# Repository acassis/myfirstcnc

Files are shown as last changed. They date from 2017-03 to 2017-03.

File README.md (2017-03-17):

# myfirstcnc
MyFirstCNC is an aluminum profile CNC:

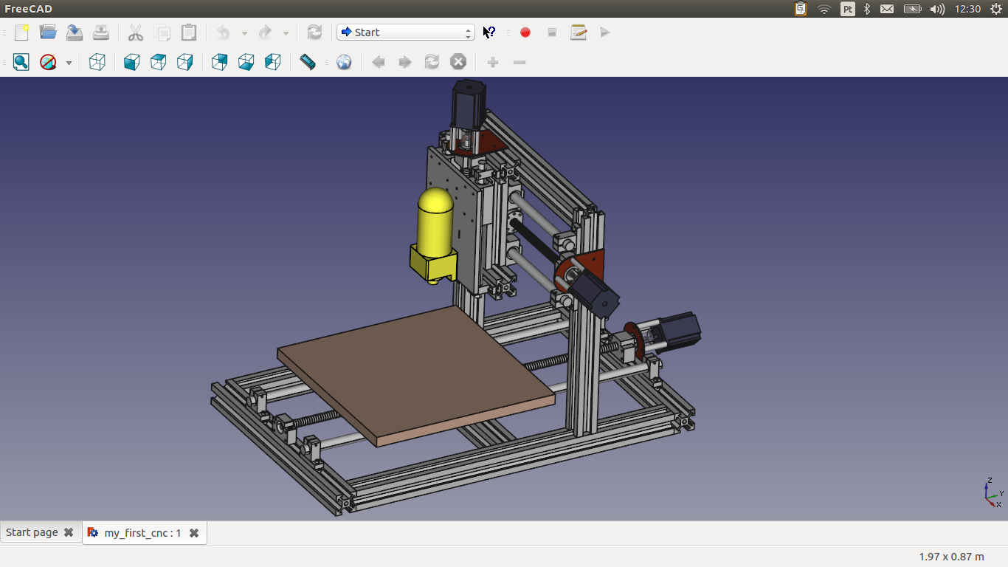
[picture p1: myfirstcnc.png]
MyFirstCNC


This CNC was designed using FreeCAD program:

https://www.freecadweb.org

Open the file Design/my_first_cnc.fcstd to see the complete
CNC machine.

Inside Design/Parts_FreeCAD/ you will find the CNC pieces that
were designed on FreeCAD and also the 2D design of parts you
will need to mill first to create your own CNC.

This project is based on Mogens Nicolaisen's CNC Router:
http://www.thingiverse.com/thing:41594

IMPORTANT NOTE: The ballnut_holder parts were based on the
ballnut housing I bought from eBay. I noticed they don't
have the exact same dimension. So, you need to double check
it before milling your ballnut_holders.

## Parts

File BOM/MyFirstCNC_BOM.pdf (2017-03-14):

Item | Quantity | Unit Price
45X45mm T-Slot:
45x45 T-Slot 180mm | 2 | $4.55
45x45 T-Slot 213mm | 2 | $5.40
45x45 T-Slot 413mm | 2 | $10.50
45x45 T-Slot 490mm | 2 | $12.40
45x45 T-Slot 503mm | 2 | $12.75
45x45 T-Slot 713mm | 2 | $18.05
M6 T-nut slot 10 | 40
M5 T-nut slot 10 | 10
| 12 | $1.38
200x230x10mm al-plate | 1 | $20.00
350x250x10mm al-plate | 1 | $30.00
SFC16 (SBR16 300mm) | 2 | $24.75
SFC20 (SBR20 500mm) | 2 | $36.96
SFC20 | 2 | $41.74
SK20 Shaft Support | 8 | $9.95
SK16 Shaft Support | 4 | $7.49
SBR16LUU (SC16WUU) | 2 | $15.50
SBR20UU (SC20VUU) | 8 | $6.91

Ballscrews RM1605:
RM1605 300mm | 1 | $42.80
RM1605 500mm | 1 | $52.30
RM1605 800mm | 1 | $170.48
| 3 | $47.42
Ball Nut Housings | 3 | $22.50
| 3 | $25.00
| 3 | $44.88
DeWalt D26670 | 1 | $99.00

Corner bracket + T-nut's and bolts

Hardened chrome-plated
shafts (Total length):

Sets BK/BF12 w/ locknuts and circlips

8mm X 8mm CNC Flexible Jaw Spider Plum Coupling

Stepper Motor 18.9Kgcm
57BYGH76-401A

6x mechanical limit switch

| 1 | RR$ 52.99
Motor Holder | 3 | R$ 9.80

Total:

2x line laser for laser crosshair

4 Axis 3.5A CNC TB6560
Stepper Motor Driver

Price | Status

$9.10
$10.80
$21.00
$24.80
$25.50
$36.10

$16.56

$20.00
$30.00

$49.50
$73.92
$83.48

$79.60
$29.96
$31.00
$55.28

$42.80
$52.30
$170.48

$142.26

$67.50

$180.00

$104.29

$99.00

$124.31

$73.50

$1,579.54 http://www.amazon.com/DEWALT-D26670-Laminate-Trim-Router/dp/B000HX6T28/www.ebay.com/itm/181028978193www.ebay.com/itm/370411712526www.ebay.com/itm/171052051646
www.ebay.com/itm/281102885725

http://www.aliexpress.com/store/product/High-quality-1pcs-SFU1605-Rolled-C7-Ball-Screw-L300mm-1pcs-Ballnut-ends-machining/714447_639644460.htmlhttp://www.aliexpress.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

http://www.ebay.com/itm/161242193610

http://www.ebay.com/itm/111221109249

http://www.ebay.com/itm/221277630019http://www.ebay.com/itm/360828125175

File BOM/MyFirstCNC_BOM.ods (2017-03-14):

Item | Quantity | Unit Price | Price | Status
45X45mm T-Slot:
45x45 T-Slot 180mm | 2 | $4.55 | $9.10
45x45 T-Slot 213mm | 2 | $5.40 | $10.80
45x45 T-Slot 413mm | 2 | $10.50 | $21.00
45x45 T-Slot 490mm | 2 | $12.40 | $24.80
45x45 T-Slot 503mm | 2 | $12.75 | $25.50
45x45 T-Slot 713mm | 2 | $18.05 | $36.10
M6 T-nut slot 10 | 40
M5 T-nut slot 10 | 10
Corner bracket + T-nut's and bolts | 12 | $1.38 | $16.56
200x230x10mm al-plate | 1 | $20.00 | $20.00
350x250x10mm al-plate | 1 | $30.00 | $30.00
Hardened chrome-plated shafts (Total length):
SFC16 (SBR16 300mm) | 2 | $24.75 | $49.50
SFC20 (SBR20 500mm) | 2 | $36.96 | $73.92
SFC20 | 2 | $41.74 | $83.48
SK20 Shaft Support | 8 | $9.95 | $79.60 |  | www.ebay.com/itm/181028978193
SK16 Shaft Support | 4 | $7.49 | $29.96 |  | www.ebay.com/itm/370411712526
SBR16LUU (SC16WUU) | 2 | $15.50 | $31.00 |  | www.ebay.com/itm/171052051646
SBR20UU (SC20VUU) | 8 | $6.91 | $55.28 |  | www.ebay.com/itm/281102885725
Ballscrews RM1605:
RM1605 300mm | 1 | $42.80 | $42.80 |  | http://www.aliexpress.com/store/product/High-quality-1pcs-SFU1605-Rolled-C7-Ball-Screw-L300mm-1pcs-Ballnut-ends-machining/714447_639644460.html
RM1605 500mm | 1 | $52.30 | $52.30 |  | http://www.aliexpress.com/store/product/1pcs-SFU1605-Ball-Screw-L500mm-1pcs-Ballnut-ends-machining/714447_648089331.html
RM1605 800mm | 1 | $170.48 | $170.48 |  | http://www.aliexpress.com/item/1pcs-SFU1605-Ball-Screw-L800mm-1pcs-Ballnut-ends-machining/648181573.html
Sets BK/BF12 w/ locknuts and circlips | 3 | $47.42 | $142.26 |  | http://www.ebay.com/itm/161242193610
Ball Nut Housings | 3 | $22.50 | $67.50 |  | http://www.ebay.com/itm/111221109249
8mm X 8mm CNC Flexible Jaw Spider Plum Coupling | 3 | $25.00 | $180.00 |  | http://www.ebay.com/itm/221277630019
Stepper Motor 18.9Kgcm 57BYGH76-401A | 3 | $44.88 | $104.29
DeWalt D26670 | 1 | $99.00 | $99.00 |  | http://www.amazon.com/DEWALT-D26670-Laminate-Trim-Router/dp/B000HX6T28/
6x mechanical limit switch
2x line laser for laser crosshair
4 Axis 3.5A CNC TB6560 Stepper Motor Driver | 1 | RR$ 52.99 | $124.31 |  | http://www.ebay.com/itm/360828125175
Motor Holder | 3 | R$ 9.80 | $73.50
Total: |  |  | $1,579.54

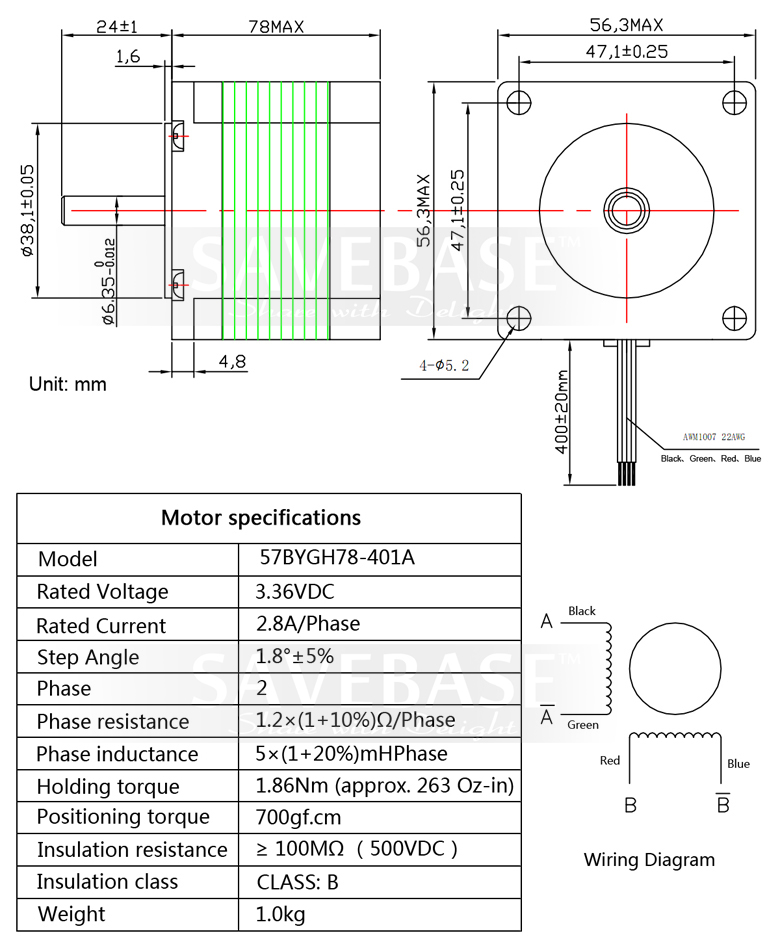
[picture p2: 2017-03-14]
Design/Parts_FreeCAD/stepper_motor/57BYGH78_401A.jpg

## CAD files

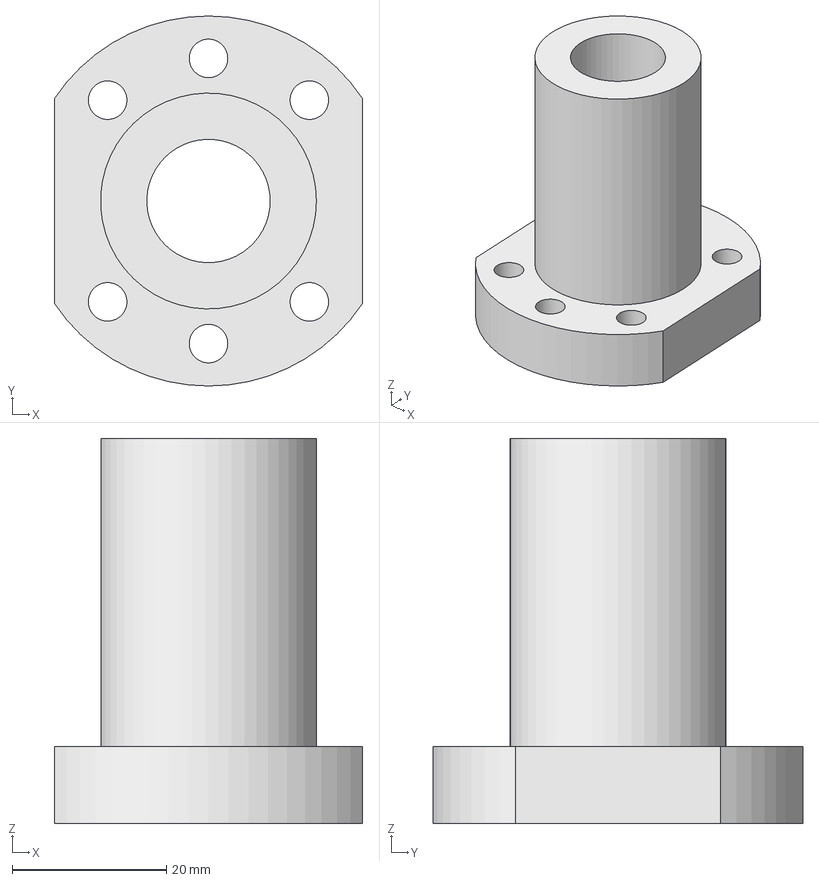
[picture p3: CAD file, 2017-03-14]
Design/Parts_FreeCAD/ballnut/ballnuts.fcstd
40.0 x 48.0 x 50.0 mm

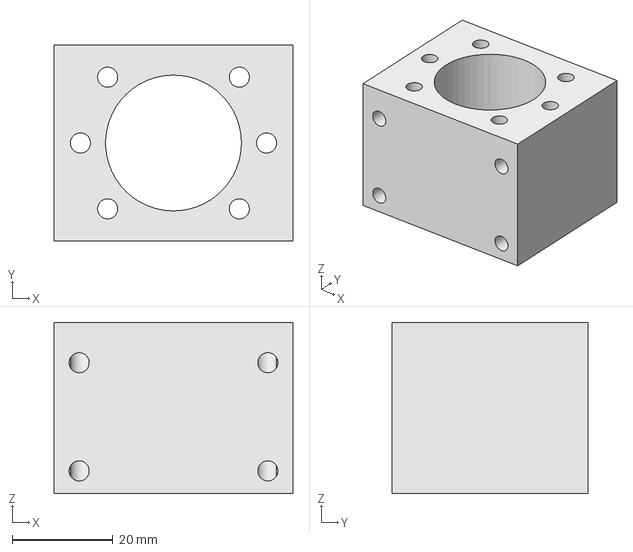
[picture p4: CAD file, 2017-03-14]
Design/Parts_FreeCAD/ballnut_house/ballnut_house.fcstd
47.5 x 39.0 x 34.0 mm

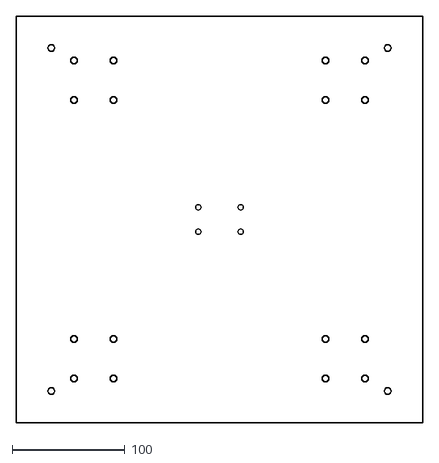
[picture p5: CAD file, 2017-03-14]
Design/Parts_FreeCAD/bed/bed_top_view.dxf
360.0 x 360.0

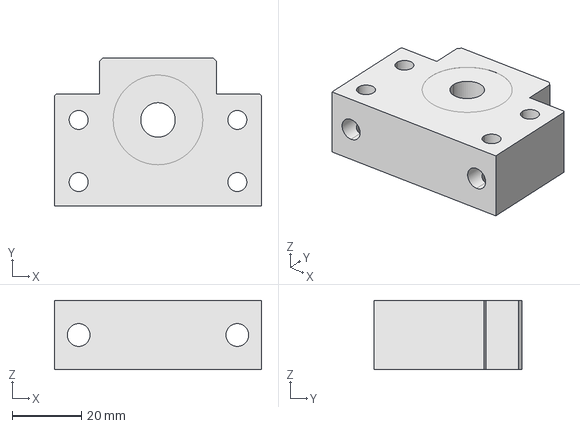
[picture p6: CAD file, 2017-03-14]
Design/Parts_FreeCAD/bf12/bf12.fcstd
60.0 x 43.0 x 20.0 mm

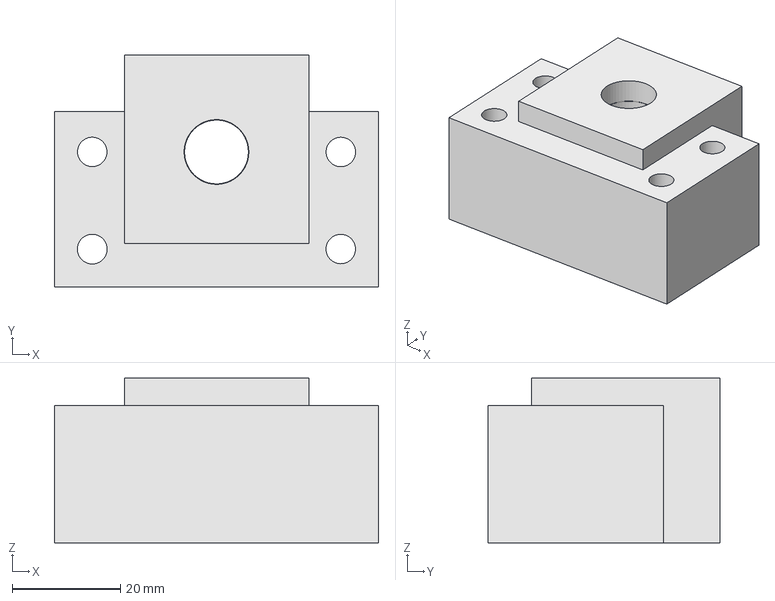
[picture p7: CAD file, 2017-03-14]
Design/Parts_FreeCAD/bk12/BK12.fcstd
60.0 x 42.9 x 30.5 mm

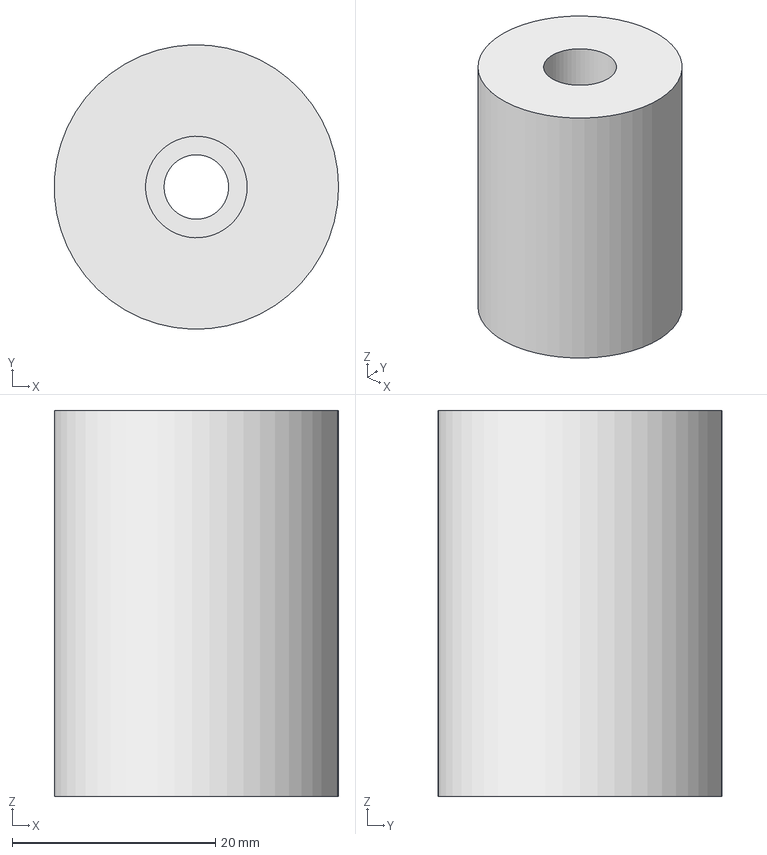
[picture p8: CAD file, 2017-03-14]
Design/Parts_FreeCAD/coupler/coupler.fcstd
28.0 x 28.0 x 38.0 mm

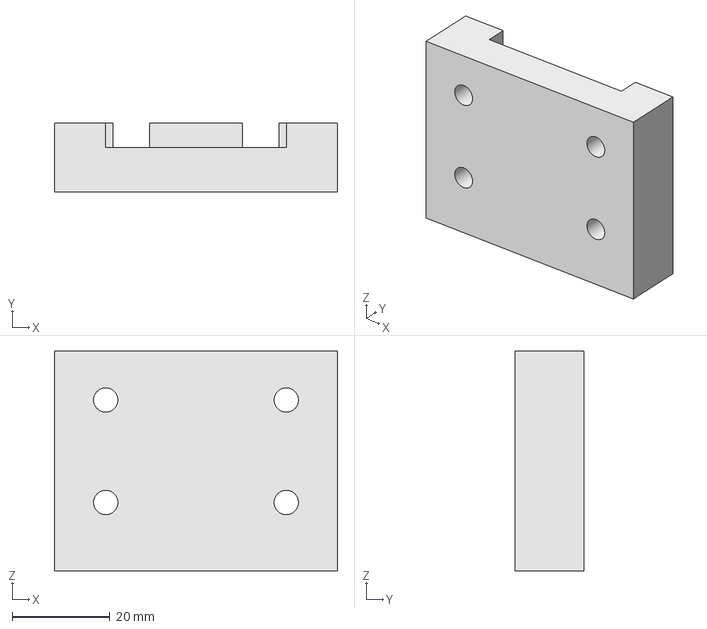
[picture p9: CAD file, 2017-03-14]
Design/Parts_FreeCAD/holder_ballnut_bed/ballnut_house_support.step
58.0 x 14.2 x 45.0 mm

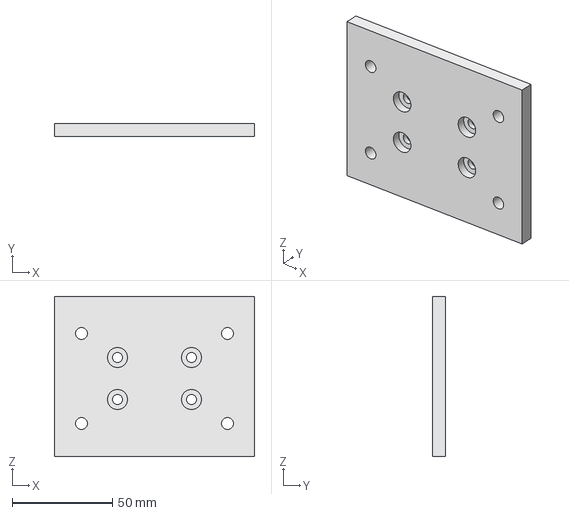
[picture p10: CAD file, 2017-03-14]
Design/Parts_FreeCAD/holder_ballnut_gantry/holder_ballnut_gantry.fcstd
100.0 x 6.50 x 80.0 mm

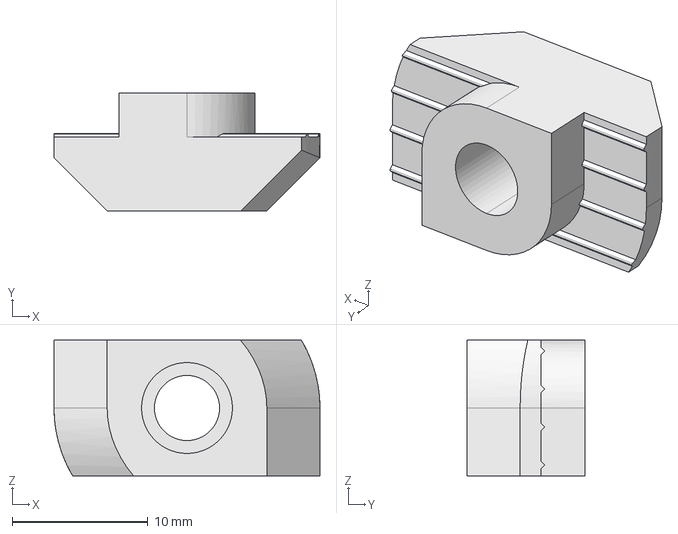
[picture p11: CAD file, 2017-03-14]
Design/Parts_FreeCAD/m6_tnut/m6_Tnut_slot10.fcstd
19.6 x 8.70 x 10.0 mm

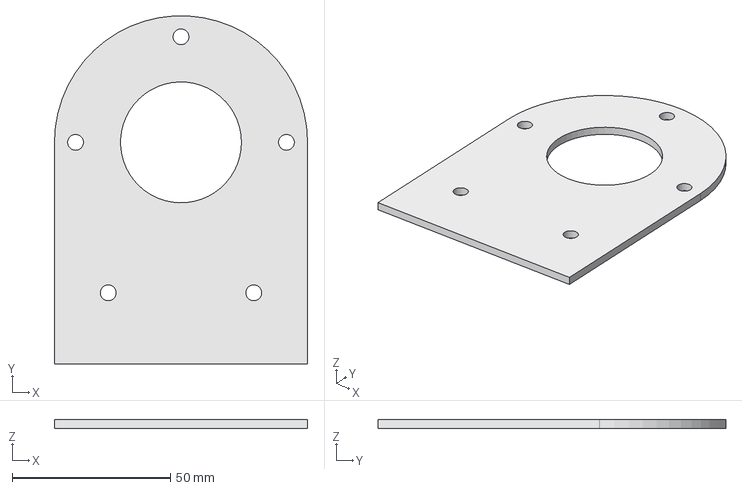
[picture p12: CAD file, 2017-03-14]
Design/Parts_FreeCAD/motor_base/motor_base.step
80.0 x 110.0 x 2.70 mm

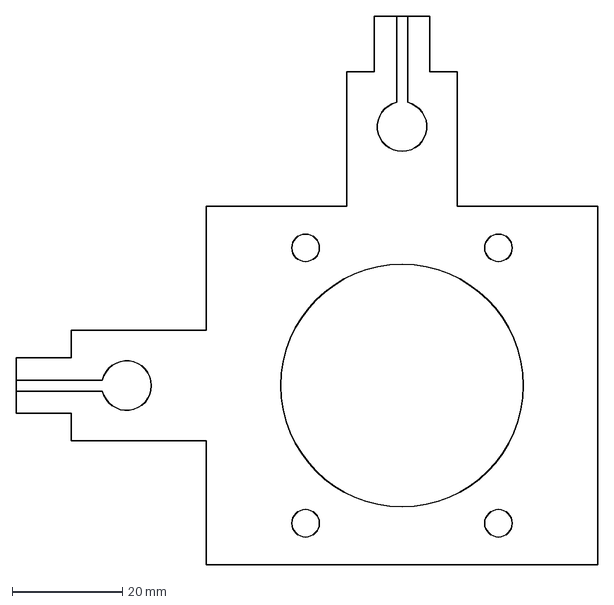
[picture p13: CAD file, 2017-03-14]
Design/Parts_FreeCAD/original/laserholder.dxf
105.5 x 99.5 mm

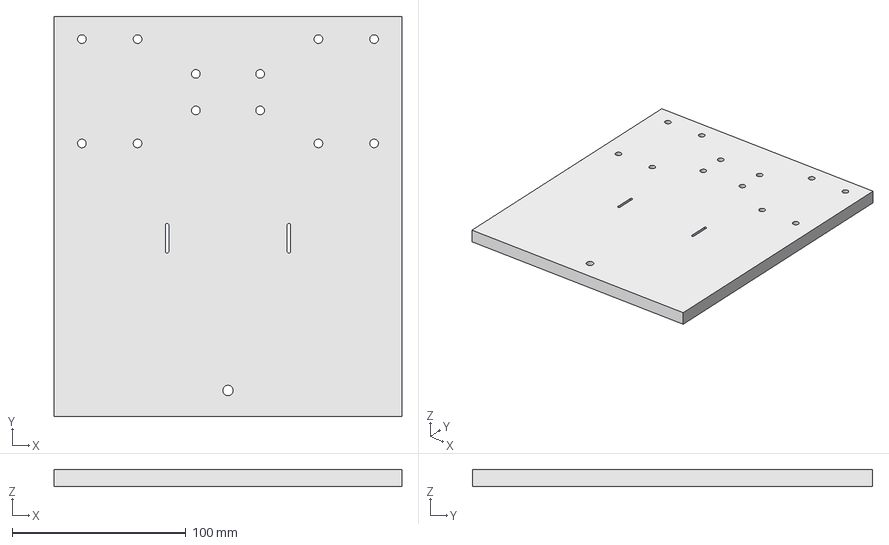
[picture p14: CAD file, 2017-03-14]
Design/Parts_FreeCAD/platez_base/platez_base.fcstd
200.0 x 230.0 x 10.0 mm

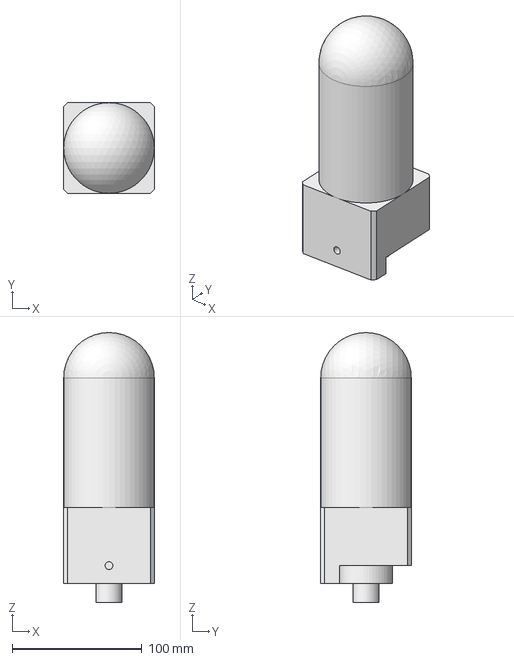
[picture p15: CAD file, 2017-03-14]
Design/Parts_FreeCAD/router/router.fcstd
70.0 x 70.0 x 208.5 mm

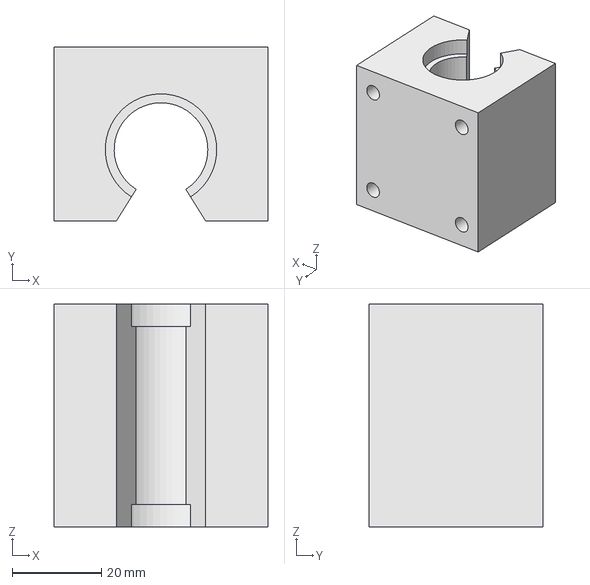
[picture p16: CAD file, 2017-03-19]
Design/Parts_FreeCAD/sbr20uu/sbr20uu.fcstd
48.0 x 39.0 x 50.0 mm

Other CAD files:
Design/Parts_FreeCAD/sc16wuu/sc16wuu.fcstd
Design/Parts_FreeCAD/sc20vuu/SC20VUU.fcstd
Design/Parts_FreeCAD/sk16/sk16.fcstd
Design/Parts_FreeCAD/sk20/sk20.fcstd
Design/Parts_FreeCAD/ballscrew/ballscrew_thread.fcstd
Design/Parts_FreeCAD/ballscrew/rm1605_800mm.fcstd
Design/Parts_FreeCAD/ballscrew/simple_ballscrew.fcstd
Design/Parts_FreeCAD/ballscrew/simple_ballscrew_300mm.fcstd
Design/Parts_FreeCAD/ballscrew_500mm/simple_ballscrew_500mm.fcstd
Design/Parts_FreeCAD/bed/bed.dwg
Design/Parts_FreeCAD/bed/bed.fcstd
Design/Parts_FreeCAD/bed/bed.step
Design/Parts_FreeCAD/holder_ballnut_bed/ballnut_house_support.dxf
Design/Parts_FreeCAD/holder_ballnut_bed/ballnut_house_support.fcstd
Design/Parts_FreeCAD/motor_base/Motor_Base.fcstd
Design/Parts_FreeCAD/motor_base/motor_base.dxf
Design/Parts_FreeCAD/original/BedAndMotorMount.dxf
Design/Parts_FreeCAD/original/pladez.dxf
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

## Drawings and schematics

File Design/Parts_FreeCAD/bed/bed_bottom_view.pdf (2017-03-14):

298mm

35mm

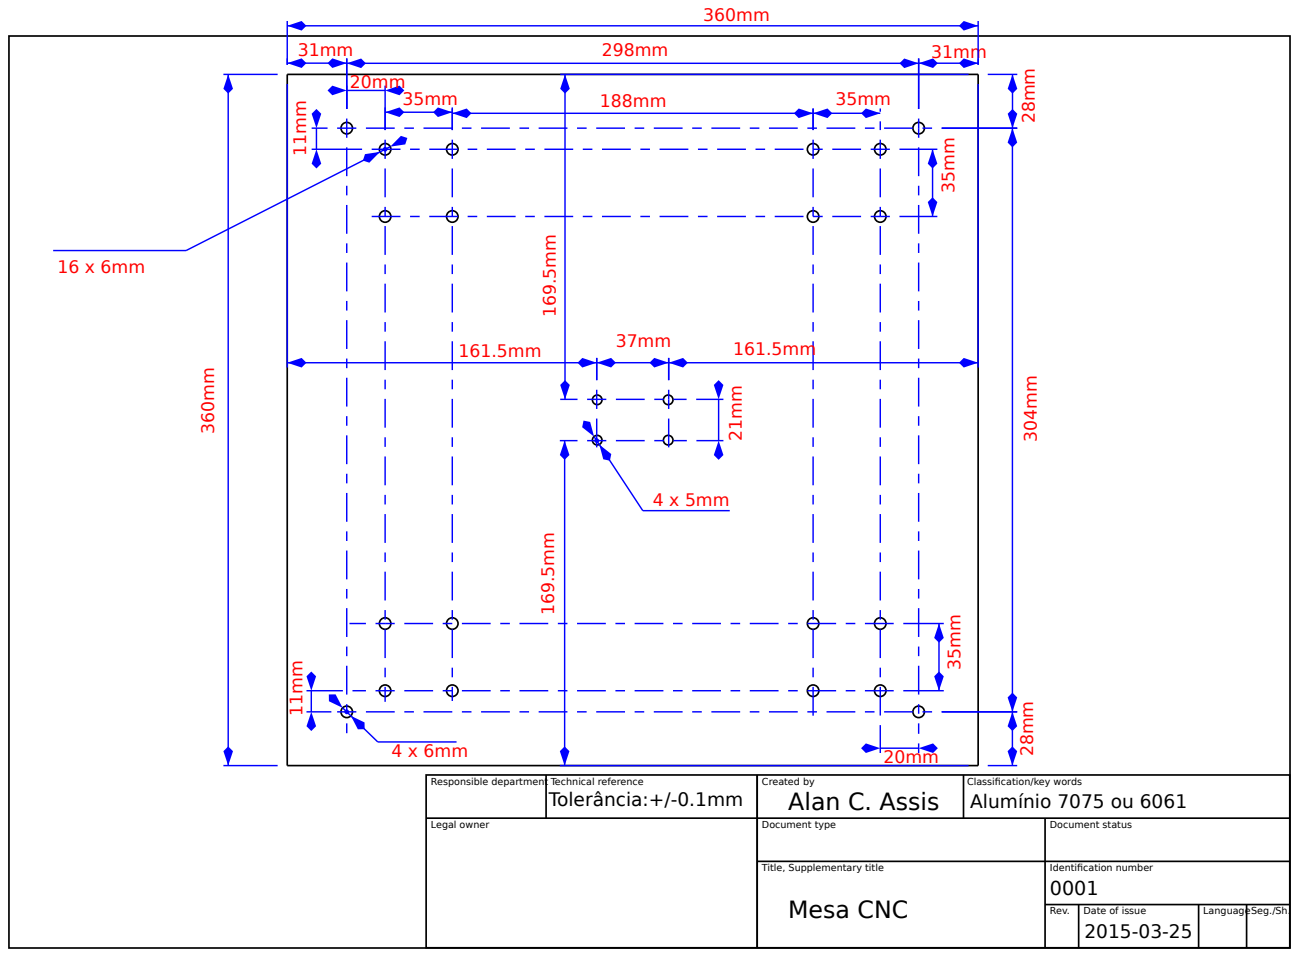
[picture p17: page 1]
161.5mm 169.5mm ¹⁶⁹.5mm; Responsible department Technical reference; Created by; Classification/key words; Legal owner; Document type; Document status; Title, Supplementary title; Identification number; Rev.; Date of issue; LanguageSeg./Sh.; Alan C. Assis; Mesa CNC; Tolerância:+/-0.1mm; Alumínio 7075 ou 6061

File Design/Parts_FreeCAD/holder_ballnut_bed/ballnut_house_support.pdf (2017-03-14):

58mm

12mm | 19mm | 12mm

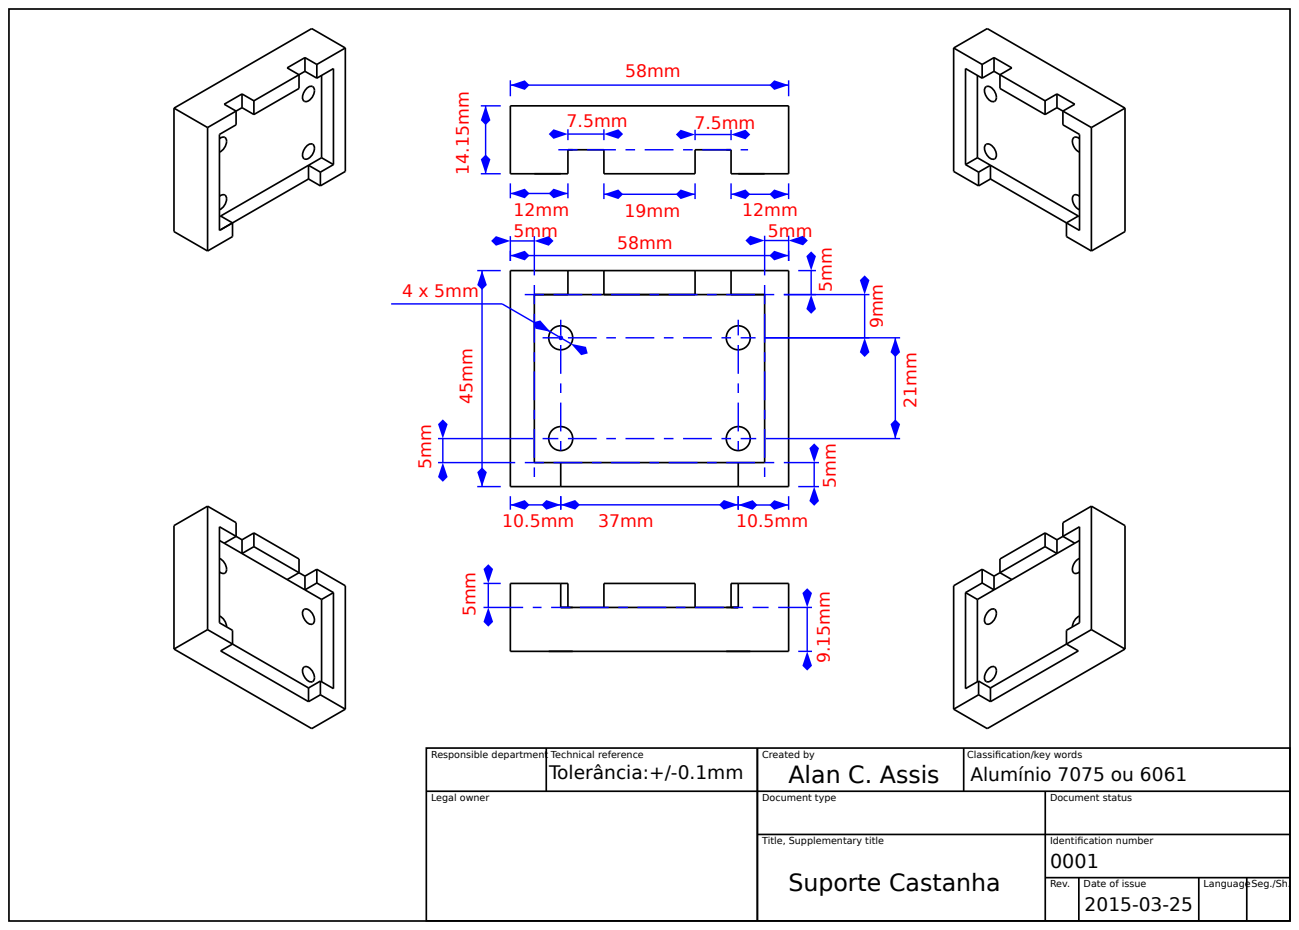
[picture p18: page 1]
Responsible department Technical reference; Created by; Classification/key words; Legal owner; Document type; Document status; Title, Supplementary title; Identification number; Rev.; Date of issue; LanguageSeg./Sh.; Alan C. Assis; Suporte Castanha; Tolerância:+/-0.1mm; Alumínio 7075 ou 6061

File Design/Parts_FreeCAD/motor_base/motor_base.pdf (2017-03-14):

33.35mm

# 5 x 5mm

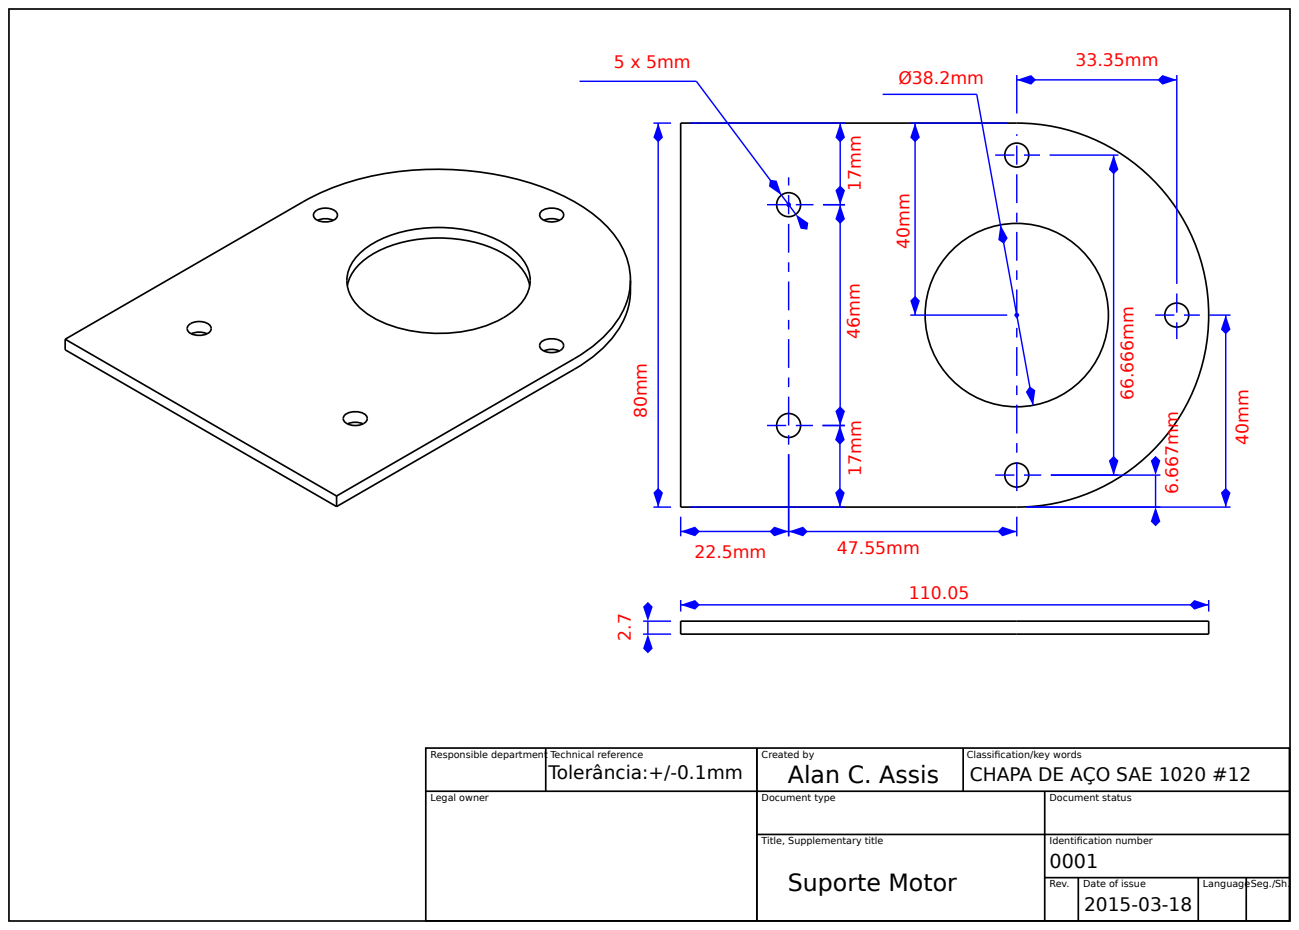
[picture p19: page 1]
Responsible department Technical reference; Created by; Classification/key words; Legal owner; Document type; Document status; Title, Supplementary title; Identification number; Rev.; Date of issue; LanguageSeg./Sh.; Alan C. Assis; Suporte Motor; Tolerância:+/-0.1mm; CHAPA DE AÇO SAE 1020 #12

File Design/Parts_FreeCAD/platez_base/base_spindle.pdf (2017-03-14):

16mm 32mm | 32mm 16mm 21mm
104mm

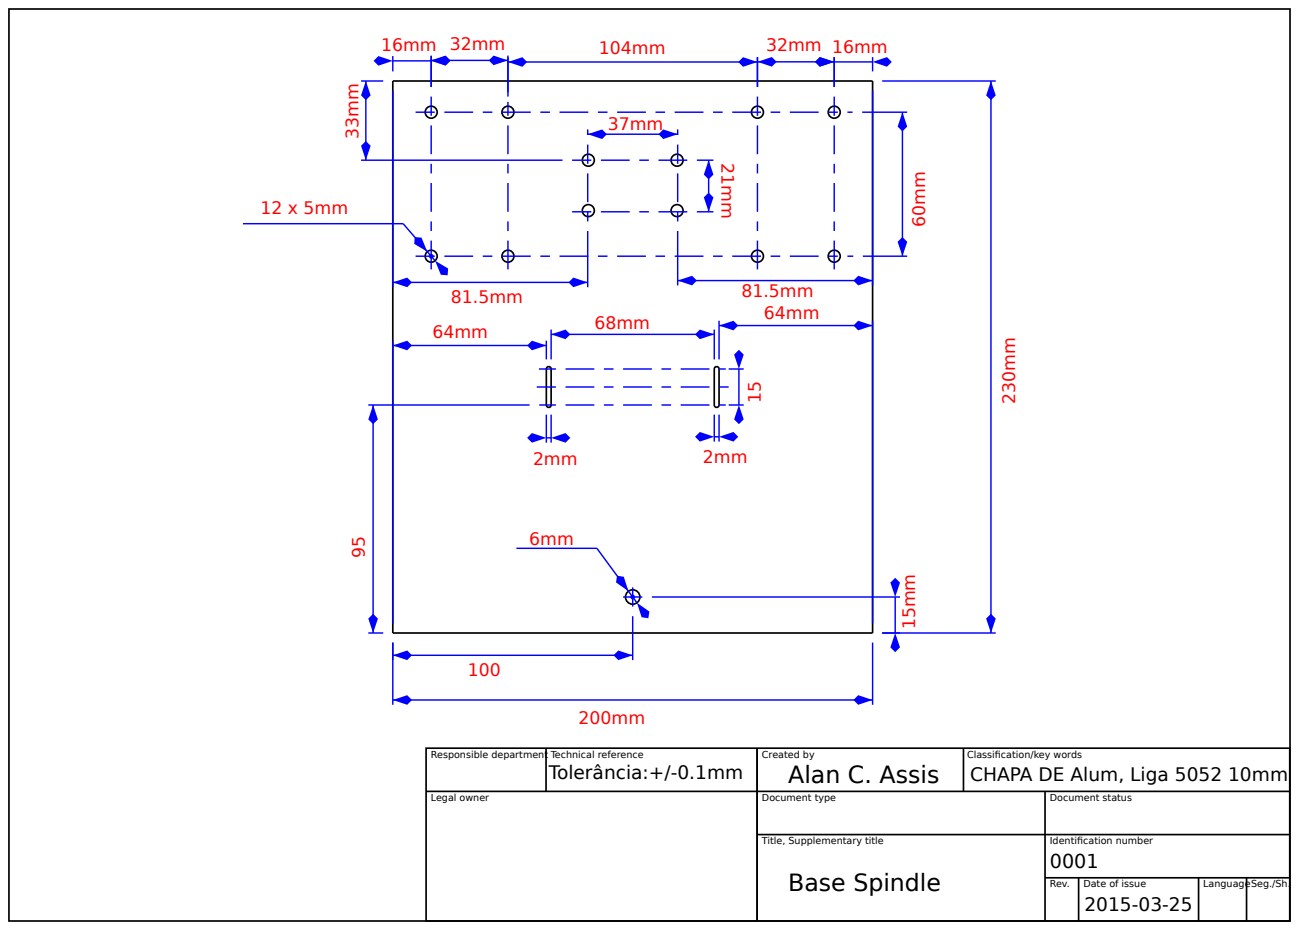
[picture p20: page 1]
Responsible department Technical reference; Created by; Classification/key words; Legal owner; Document type; Document status; Title, Supplementary title; Identification number; Rev.; Date of issue; LanguageSeg./Sh.; Alan C. Assis; Base Spindle; Tolerância:+/-0.1mm; CHAPA DE Alum, Liga 5052 10mm

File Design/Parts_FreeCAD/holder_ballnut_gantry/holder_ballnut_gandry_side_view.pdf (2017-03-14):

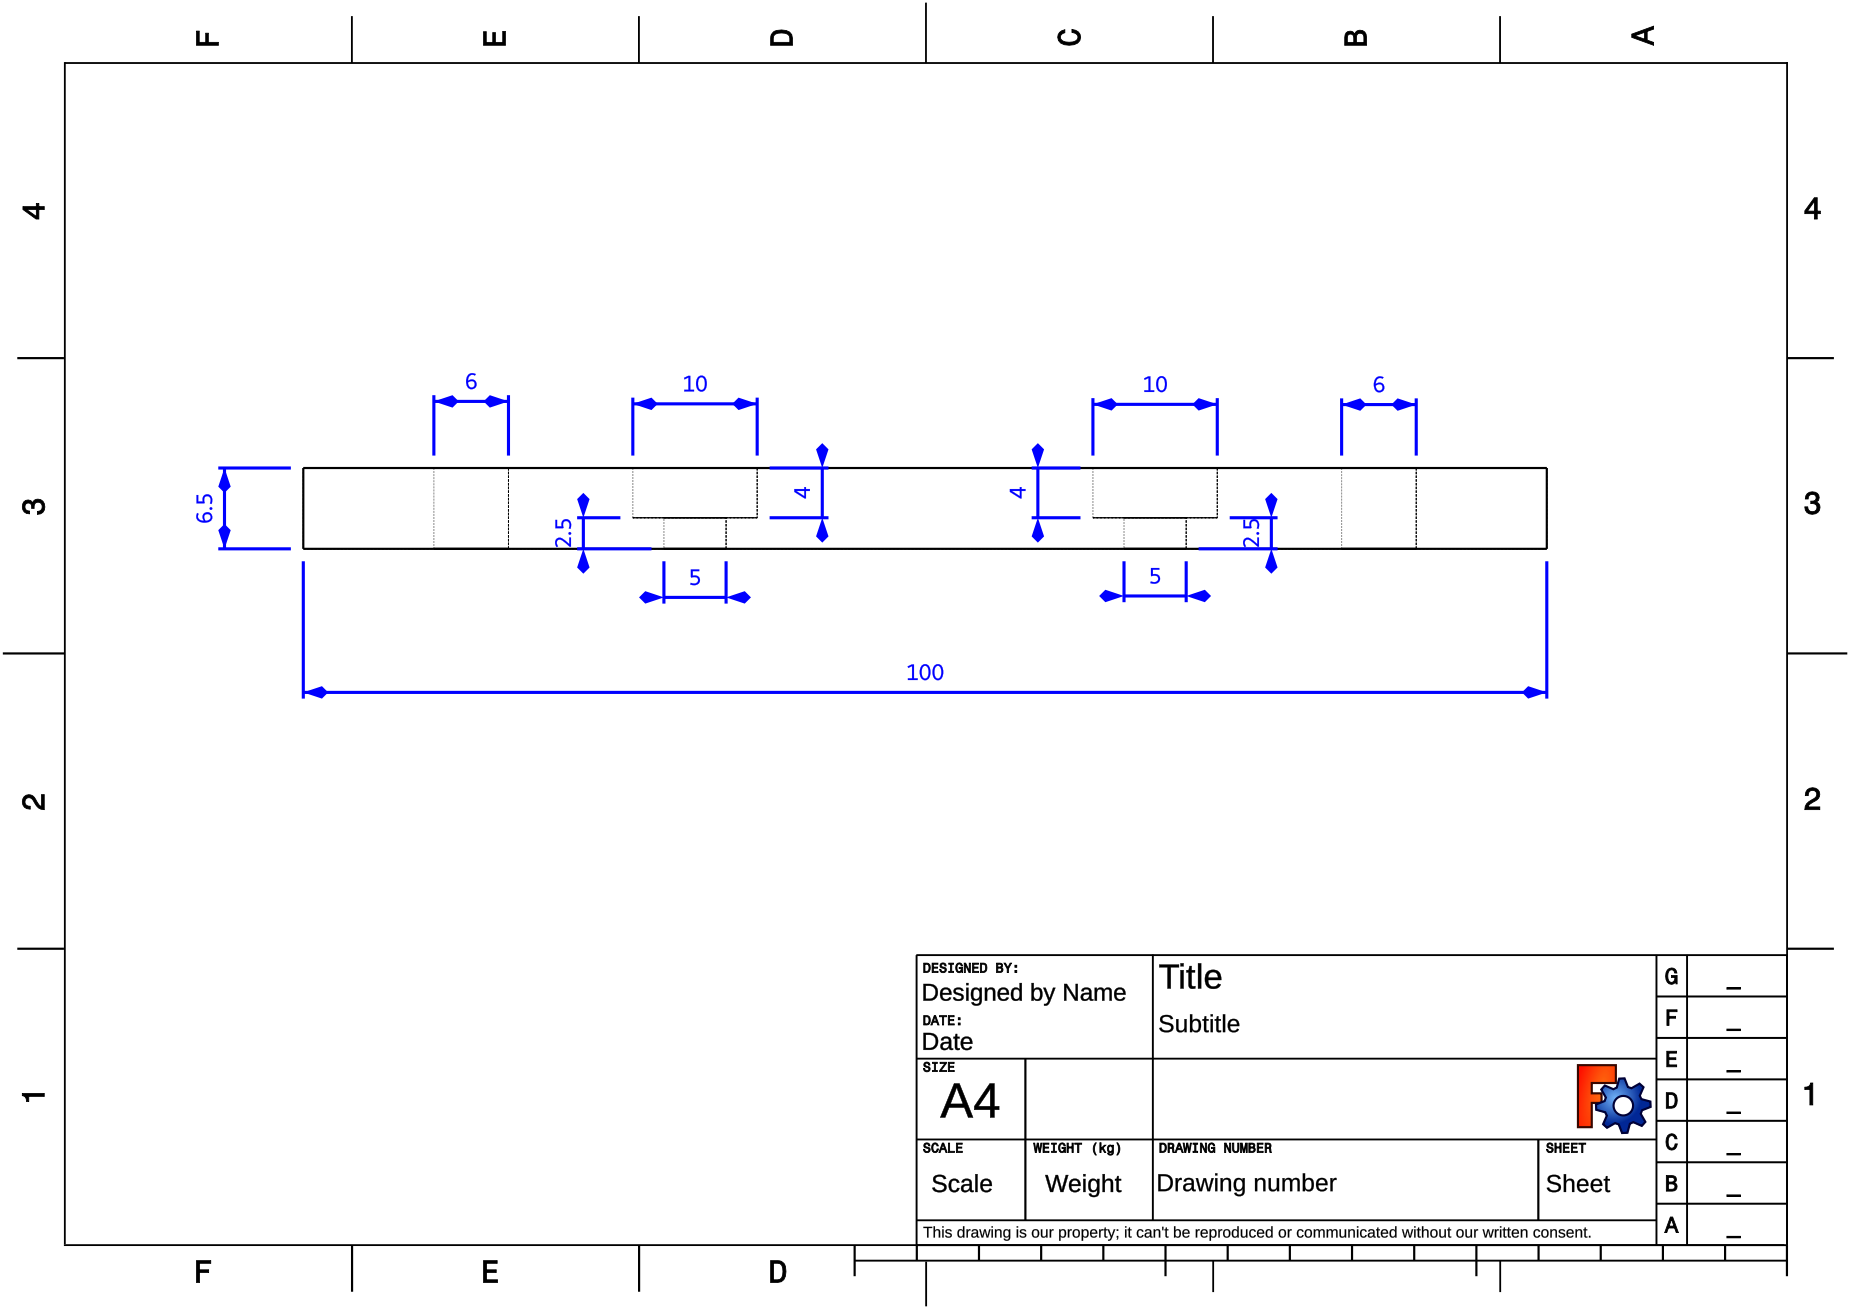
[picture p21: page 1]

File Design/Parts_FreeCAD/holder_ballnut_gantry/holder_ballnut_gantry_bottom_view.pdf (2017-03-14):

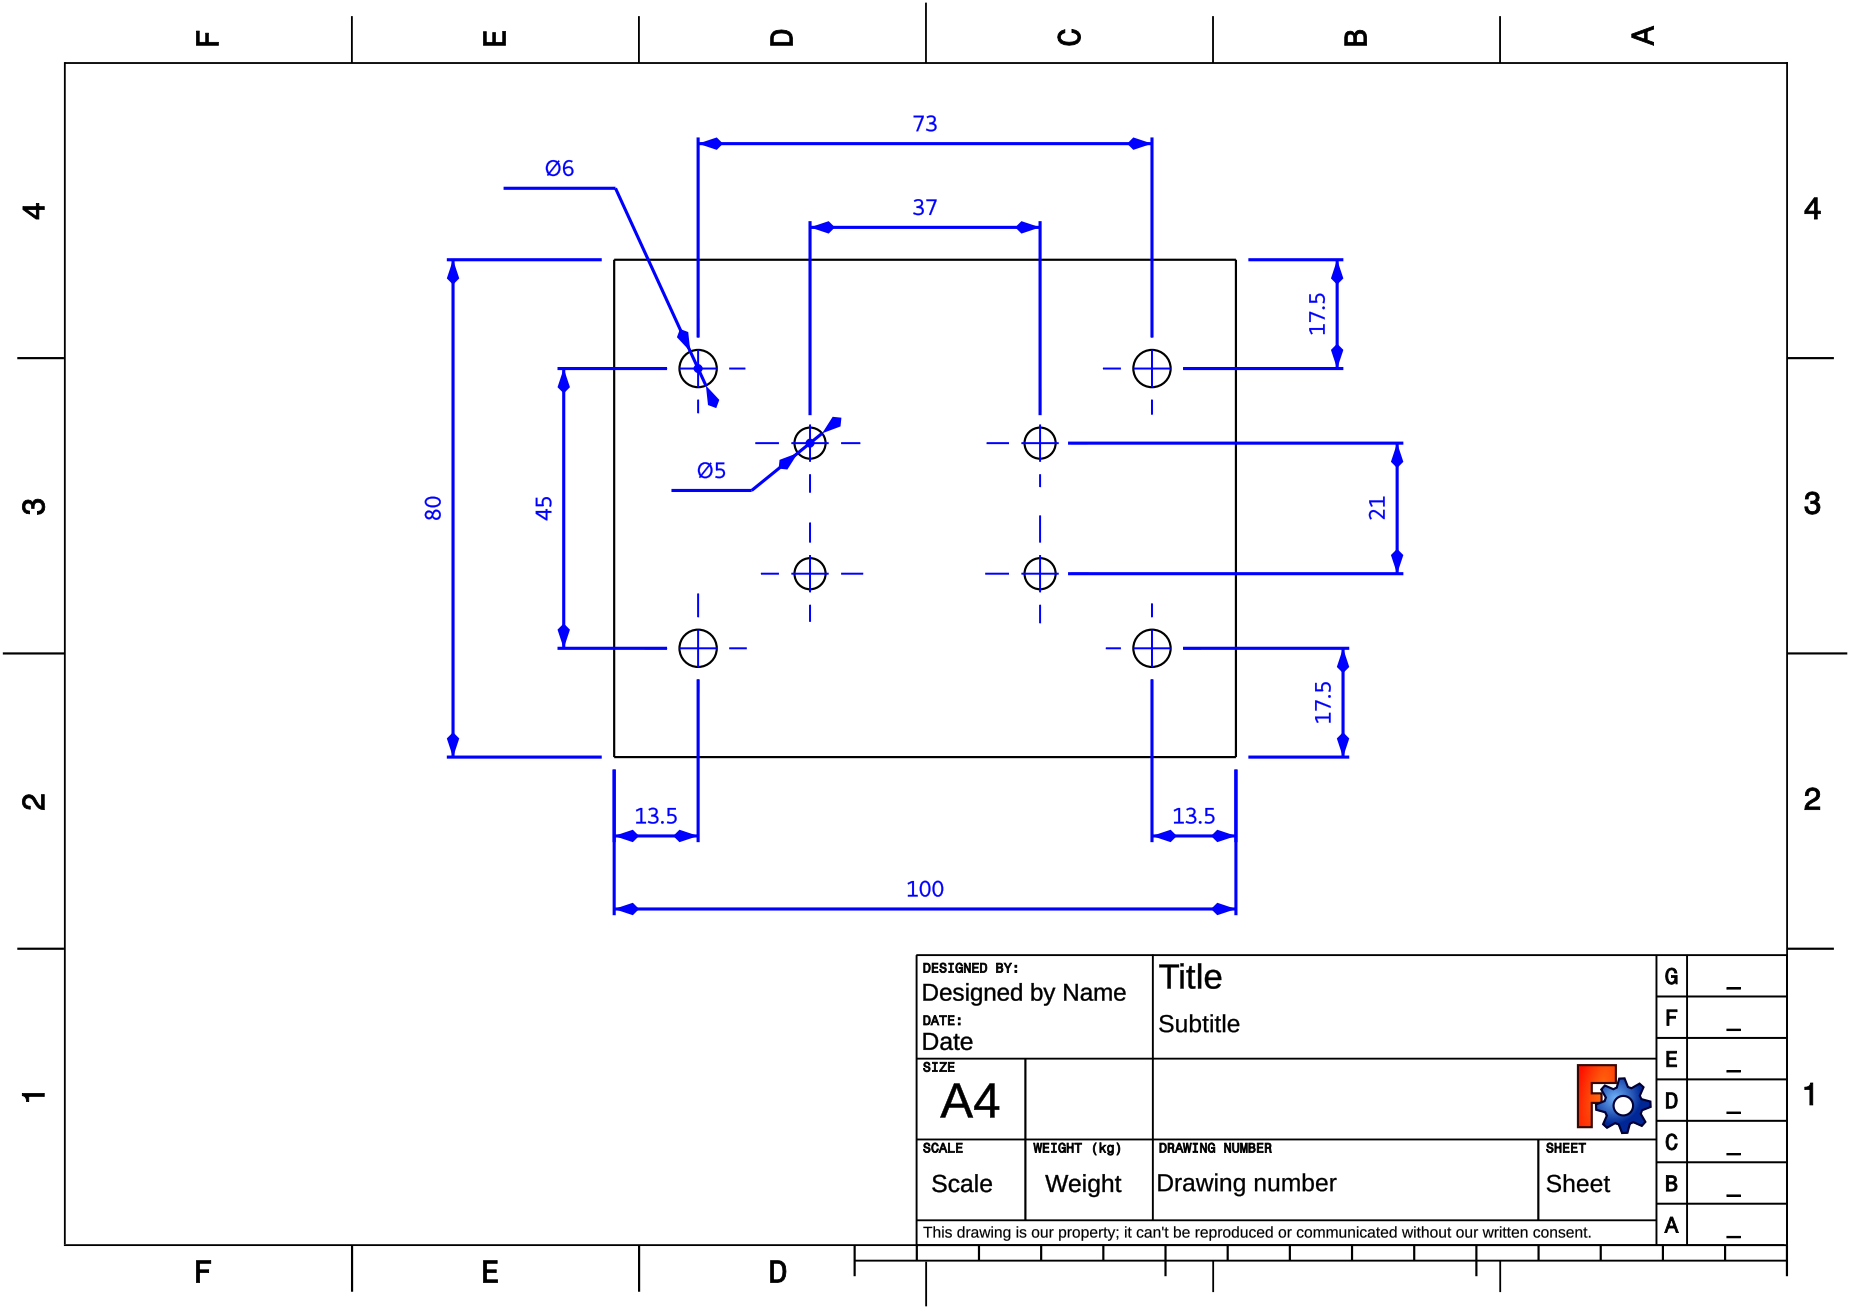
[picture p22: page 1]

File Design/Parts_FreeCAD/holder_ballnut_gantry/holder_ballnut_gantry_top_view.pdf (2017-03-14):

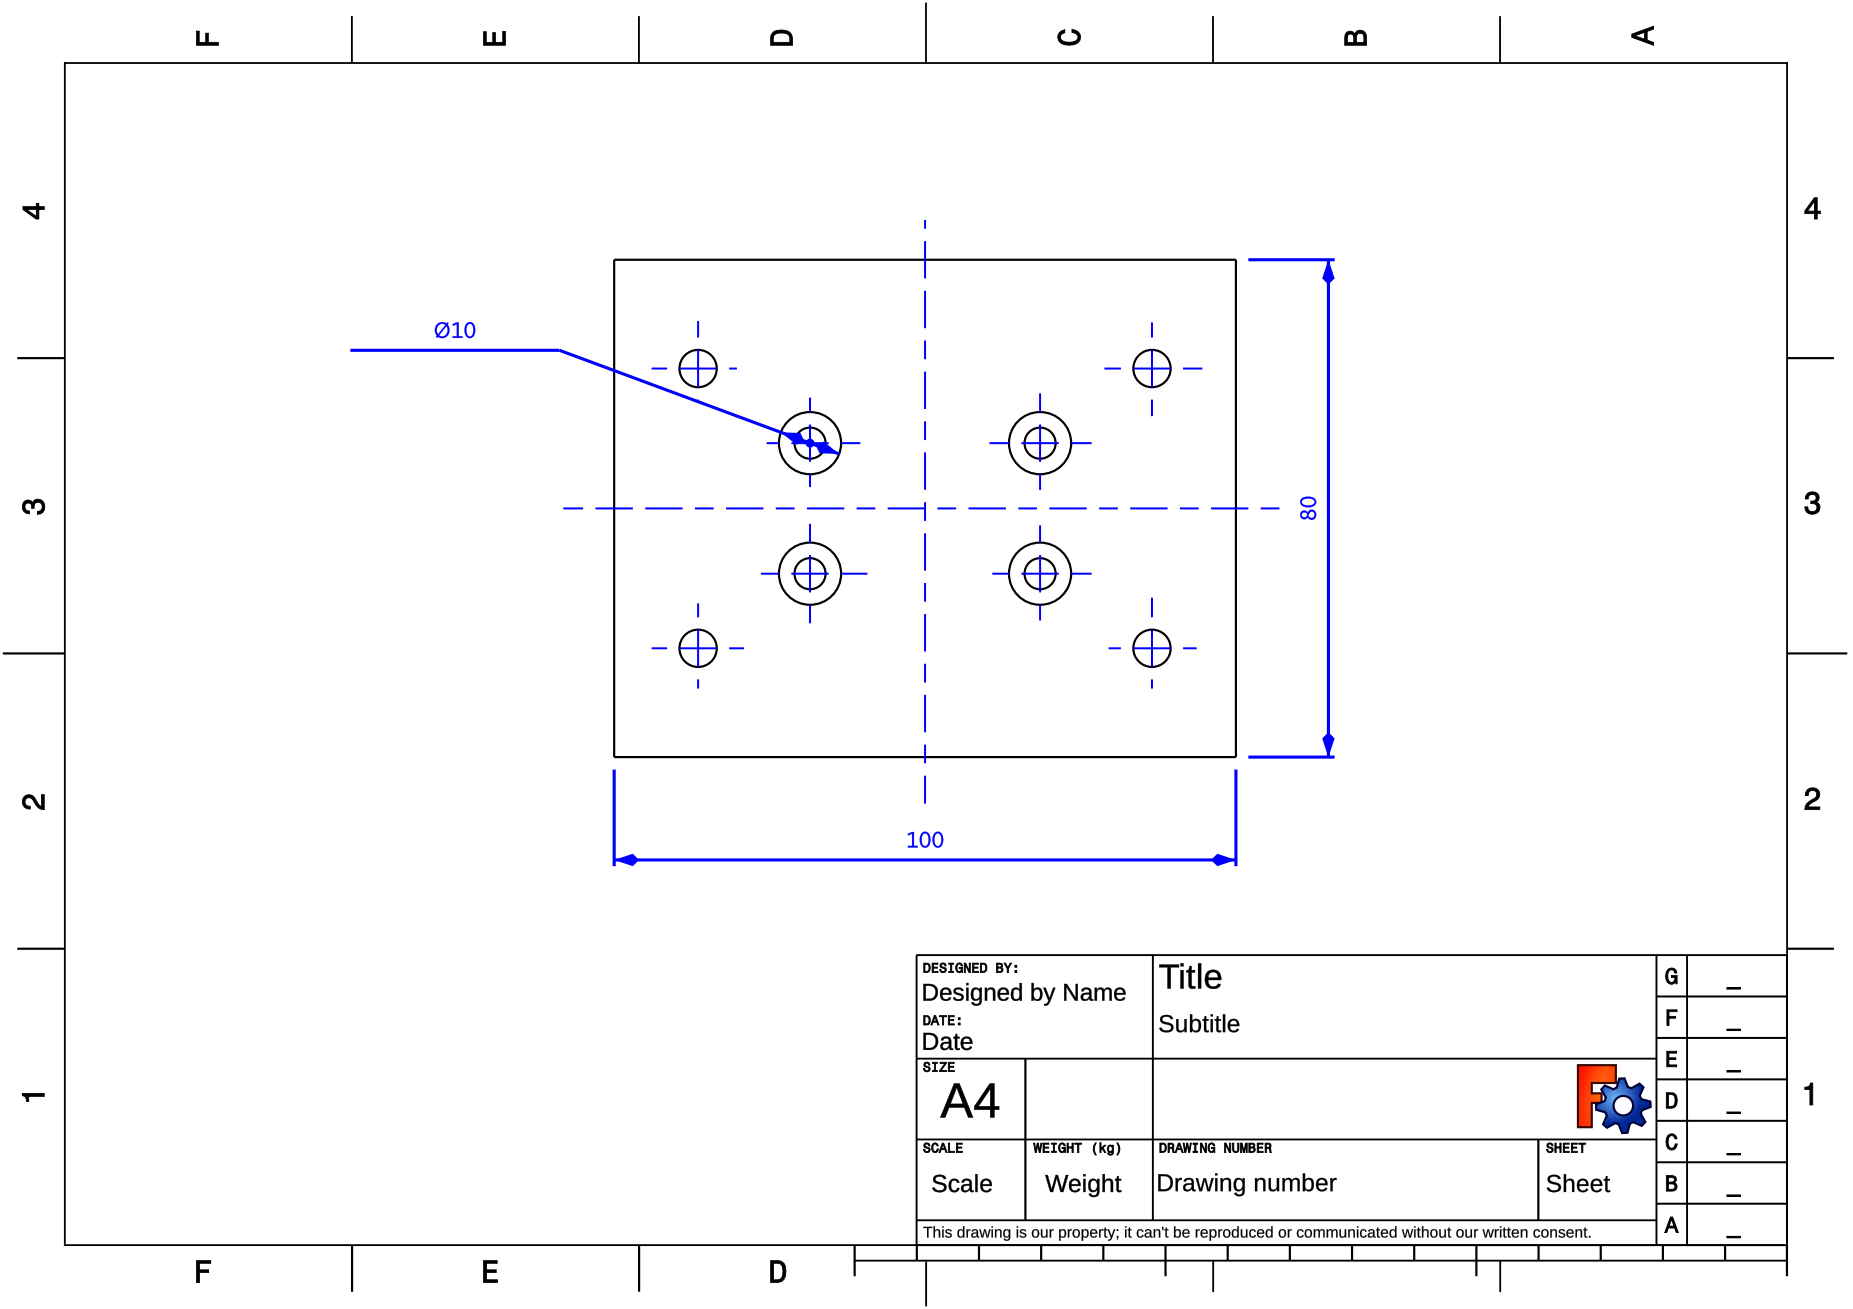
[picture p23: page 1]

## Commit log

2017-03-14 Add Design files of MyFirstCNC
    [BK12.fcstd, BedAndMotorMount.dxf, Motor_Base.fcstd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]
2017-03-14 Add Bill Of Materials
    [MyFirstCNC_BOM.ods]
2017-03-19 Add SBR20UU part design
    [sbr20uu.fcstd]
